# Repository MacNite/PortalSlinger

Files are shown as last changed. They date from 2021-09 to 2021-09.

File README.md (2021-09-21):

# PortalSlinger
PortalSlinger is an OpenSource Large Format 3D printer. The Idea was to built a large format 3D printer in the most affordable way without sacrificing to much performance. I've tested successfully teste print speeds of up to 100mm/s.

# supported by https://www.cr-3d.de

* Built Volume: 	850 mm x 400 mm x 280 mm
* Frame:          Aluminium Extrusion 3060 Slot 8
* Hotend:       	Trianglelab Volcano, Nozzle 0.8mm
* Filament:     	1,75mm, PLA & PETG
* Extruder:     	Bondtech BMG
* Bed Leveling: 	Mesh Bed Leveling with BLTouch
* Built Plate:    Caste Aluminium Plate, t = 10mm
* Print Surface:  ULTEM PEI 1000
* Heated Bed:   	2x 750W (total 1500W), 230V, up to 100C
* Connectivity:  	7“ Touch Screen, Wifi
* Controller:   	Duet Wifi
* PSU:          	Meanwell LRS-350-24
* Current Draw: 	< 8 A / < 1850 W, filtered C14 inlet with 5x20 (10A) Fuse
* Coldend Fan:  	40x20mm, 24V axial fan
* Partcooling   	4010, 24V radial fan (2 Pcs)
* Electronic:   	PSU fan and 4020 radial fan
* Linear Motion:  x: MGN12H (L=475mm), Y: HGH15CA (L=1000mm), Z: 10mm smooth rod with LMK10LUU
* Axis Movement:  x & y: 10mm GT2 belts, z: TR10x2 spindle

Find the Fusion360 model for your viewing/download pleasure here (you can download the F360 model through this link as well):

https://a360.co/3zzRa0U

.stp / .iges Files are not provided via GITHUB because they are to large (more than 25mb). You can download .stp / .iges files via the Autodesk Fusion 360 link provided above.

There is an untested / unbuilt beta-Version-CAD-Model available - this is only for "what is to come", major changes include re-positioning of y-belts, different tool head (not yet desgined) and MGN9H rails for the z-axis. Proceed with caution! https://a360.co/2XAqKi2

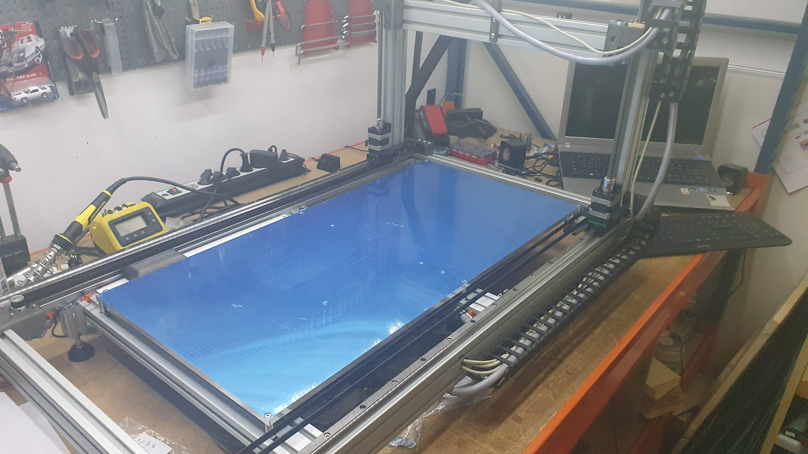
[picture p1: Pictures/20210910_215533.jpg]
PortalSlinger


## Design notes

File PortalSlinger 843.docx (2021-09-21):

# Technische Dokumentation

# Portal Slinger 843

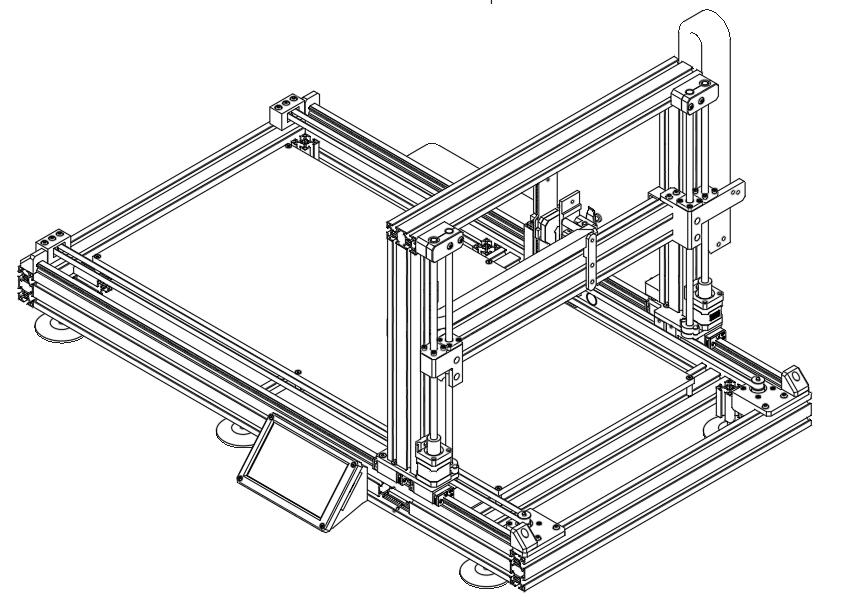
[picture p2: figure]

# 1. Technische Daten

Bauraum | 850 mm x 400 mm x 280 mm
Bauart Rahmen | Aluminium-Profile 3060 Nut 8
Hotend | Trianglelab Volcano, Düse 0.8mm
Filament | 1,75mm, PLA & PETG
Extruder | Bondtech BMG
Bed Leveling | Mesh Bed Leveling mit BLTouch (CE)
Bauplattform | Aluminium Plangefräst, t = 10mm
Druckoberfläche | ULTEM PEI 1000
Heizbett | 2x 750W (insg. 1500W), 230V, bis ca. 90°C
Konnektivität: | 7“ Touch Screen, Wifi
Steuerkarte | Duet Wifi
Netzteil | Meanwell LRS-350-24
Leistungsaufnahme | < 8 A bzw < 1850 W, C14 Kaltgerätebuchse mit Filter und 5x20 (10A) Sicherung
Coldend Lüfter | 40x20mm, 24V Axial-Lüfter
Bauteilkühlung | 4010, 24V Radial-Lüfter (2 Stk.)
Elektronik Kühlung | Integrierter Lüfter Netzteil 4020, 24V Radial-Lüfter
Linearführungen | X: MGN12H Y: HGH15CA Z: 10mm Welle mit LMK10LUU

# 2. Verkabelung des Druckkopfes

Kabelbelegung
y-Gantry | | | | | | Kabel
Stepper z1 | A+ | A- | B+ | B- | | Unitronic LIYY 4x0,34
| braun | grün | gelb | weiß
Stepper z2 | A+ | A- | B+ | B- | | Unitronic LIYY 4x0,34
| braun | grün | gelb | weiß
Stepper x | A+ | A- | B+ | B- | | Unitronic LIYY 4x0,34
| braun | grün | gelb | weiß
Stepper e0 | A+ | A- | B+ | B- | | Ölflex YSLY-JZ 25x0,5
| 4 | 5 | 6 | 7
Filament Runout | 5V | GND | S
| 21 | 22 | 23
F0 | 24V | GND
| 8 | 9
F1 | 24V | GND
| 19 | 20
H0 | 24V | GND
| 2 & 3 | 12 & 13
T0 | S | S
| 10 | 11
BLTouch | 5V | GND | Control | S | GND
| 14 | 15 | 16 | 17 | 18

# 3. Ersatzteile

Pos | Bauteil | Bestell-Link | alternativ
1 | Hotend, E3D V6, 24V, 1.75mm | https://s.click.aliexpress.com/e/_AeW5l4 | https://e3d-online.com/products/volcano-hotend
2 | BLTouch (ABL) | https://s.click.aliexpress.com/e/_A2BXyi | https://www.3djake.de/antclabs/bltouch-nivellierungssensor
3 | SSR (2 Stück) | https://www.cr3d.de/produkt/solid-state-relais-10a/ | -
4 | Extruder Bondtech BMG | https://s.click.aliexpress.com/e/_AneSdo | https://www.cr3d.de/produkt/xtruder/
5 | GT2 Idler, 25 Zähne, Riemen w=10mm, Bohrung 5mm, mit Zähnen (3 Stück) | https://s.click.aliexpress.com/e/_Aq2wyQ | -
6 | GT2 Pulley, 25 Zähne, Riemen w=10mm, Bohrung 5mm, mit Zähnen | https://s.click.aliexpress.com/e/_AfUzRY | -
7 | Zahnriemen GT2, B=10mm, L = 6 m | https://s.click.aliexpress.com/e/_9HzY4A | -
8 | Führung x-Achse (MGN12H, L = 475mm) | https://de.aliexpress.com/item/32829826159.html?spm=a2g0s.8937460.0.0.145d2e0eUGBRX5 | -
8 | Führung y-Achse (HGR15 CA, 2 Stück, L = 1000mm) | https://de.aliexpress.com/item/32961758272.html?spm=a2g0s.8937460.0.0.68d82e0e5REzLT | -
9 | Display PanelDue 7i | https://s.click.aliexpress.com/e/_9uxG9o
10 | Controller Duet Wifi | https://s.click.aliexpress.com/e/_A2KRGw | https://www.cr3d.de/produkt/duet-2-wifi/
11 | Silikon Heizmatte ( 2 Stück, 220V, 750W, Schwarz, 400x400mm) | https://s.click.aliexpress.com/e/_9j0cQE | -
12 | NEMA17 Schrittmotor (17HS15-1504S-X1) | https://s.click.aliexpress.com/e/_AU5lhU | -
13 | Druckoberfläche ULTEM PEI1000 850x410mm, nur auf Anfrage | https://www.muellerbestellung.de/TC00421-3D-ES-Ultem-1000-Polyetherimid-3D-Druck-Folie-Schwarz-einseitig-selbstklebend

# 4. Riemenspanner

x-Achse:

Wenn man „vor“ dem Drucker steht (auf der Seite mit Display und Kaltgeräteanschluss) auf der Rückseite des Tool-Heads, M5 Linsenkopfschraube. Kann mit einem 2,5mm Inbusschlüssel nachgezogen werden.

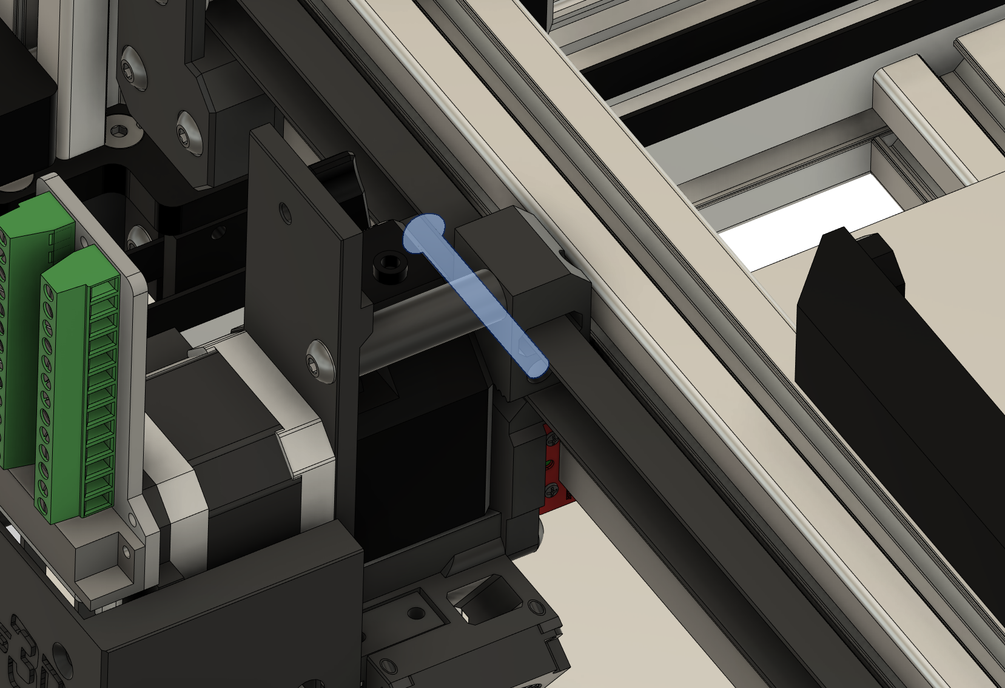
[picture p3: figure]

y-Achse:

Unterhalb des Portals auf beiden Seiten. M5 Linsenkopfschraube. Kann mit einem 2,5mm Inbusschlüssel nachgezogen werden.

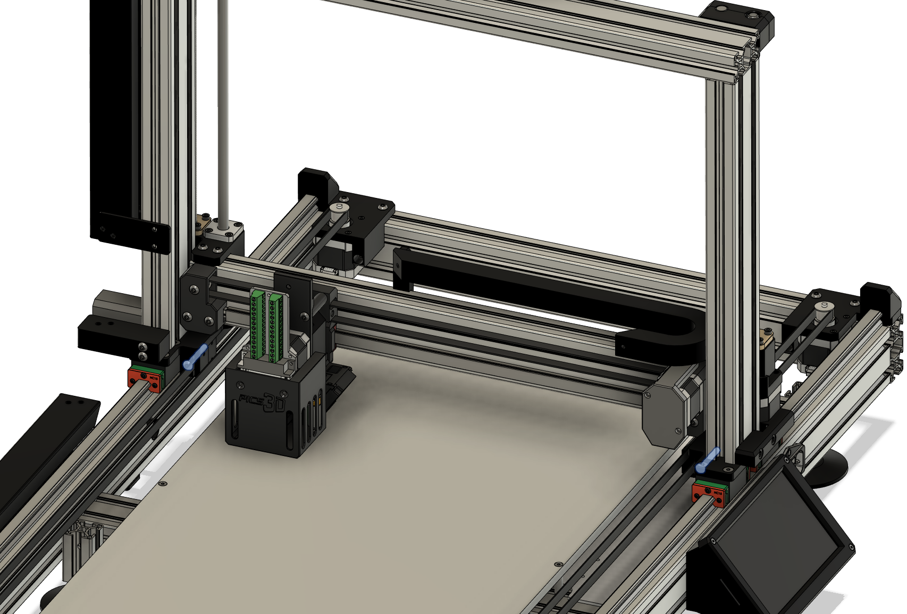
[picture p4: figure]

# 5. Druckdateien und Source-Files

Falls mal etwas am Drucker defekt ist und neu gedruckt oder anders gefertigt werden muss, sind die zugehörigen Dateien auf der Github-Seite zu finden:

https://github.com/MacNite/PortalSlinger

5 M. Nitschke Stand: 21.09.2021

Portal Slinger 843 3D Drucker – Dokumentation

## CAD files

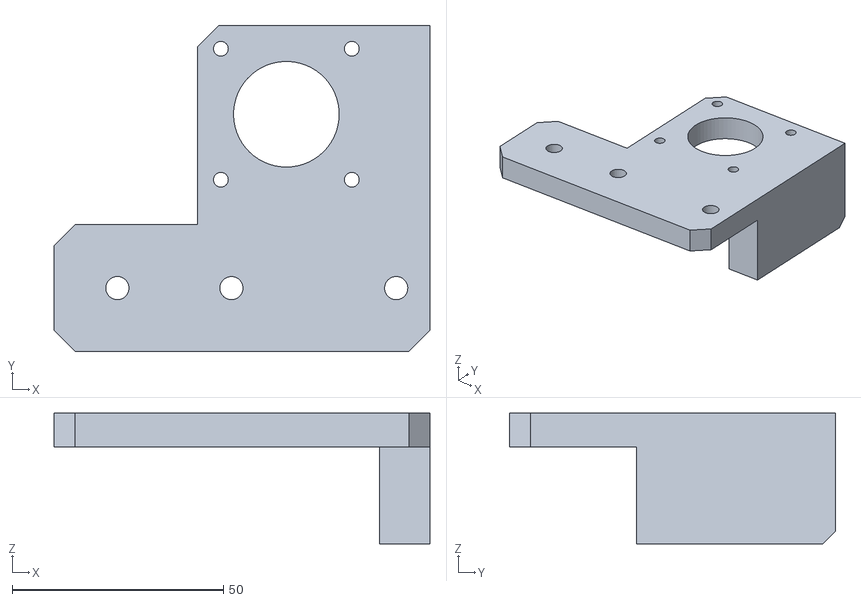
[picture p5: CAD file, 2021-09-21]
STL/y_Stepper_Mount_B_x1.stl
89.0 x 77.2 x 31.0

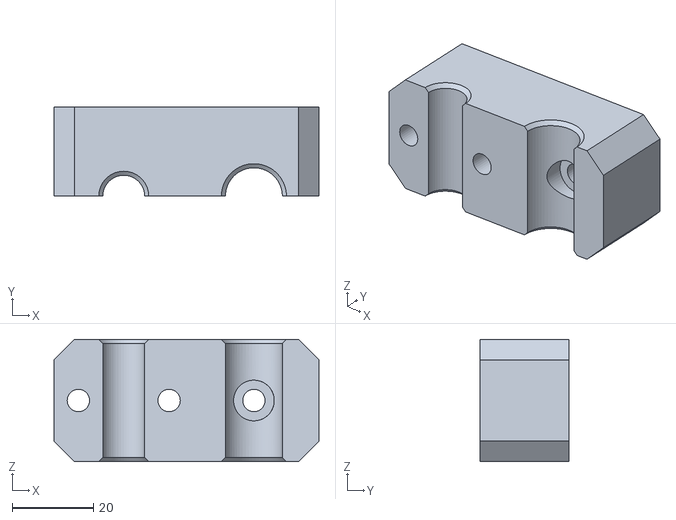
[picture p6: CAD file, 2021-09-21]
STL/z_Rot_Top_Mount_A_x2.stl
65.1 x 22.0 x 30.0

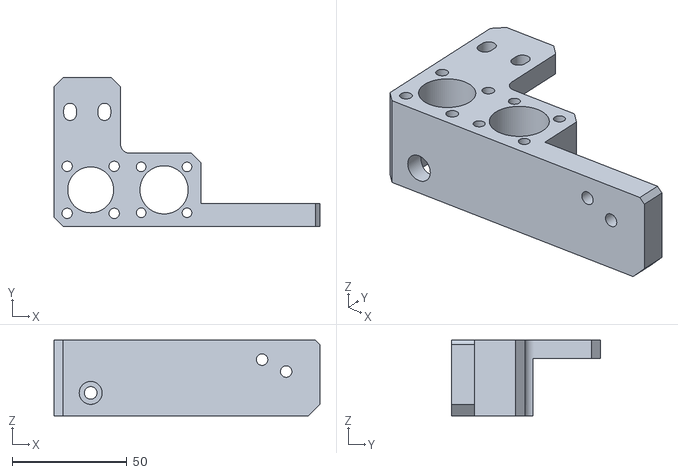
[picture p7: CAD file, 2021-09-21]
STL/z_Carriage_A_x1.stl
116.0 x 65.0 x 33.0

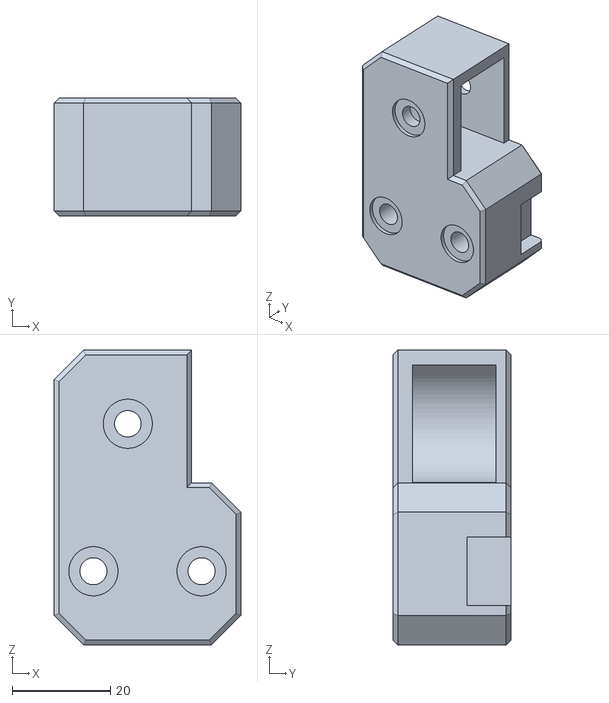
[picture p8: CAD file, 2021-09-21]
STL/x_Idler_Mount_x1.stl
38.0 x 24.0 x 60.0

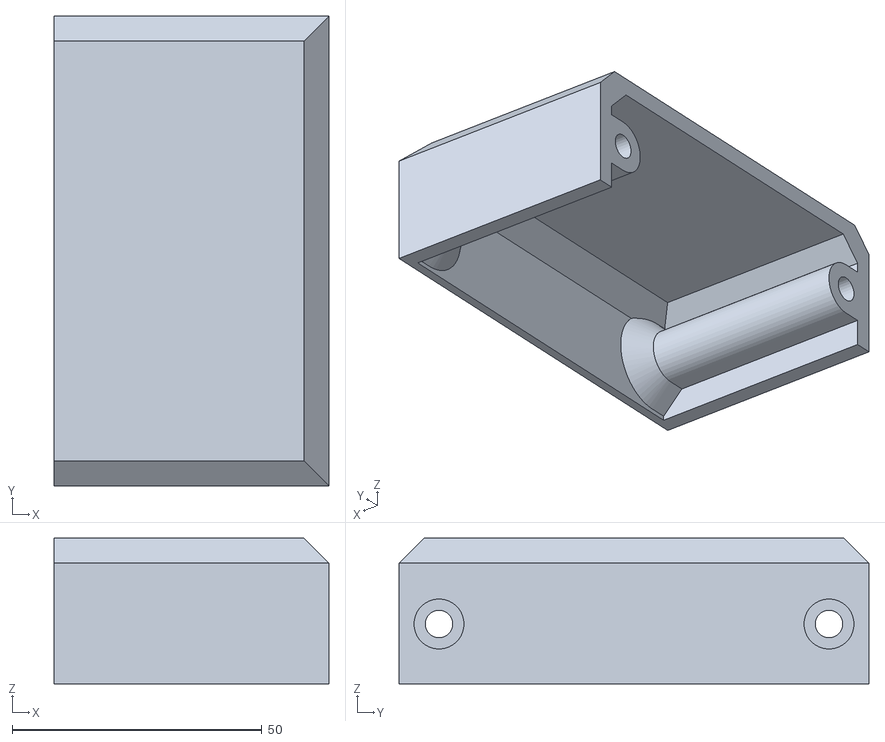
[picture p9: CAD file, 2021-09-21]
STL/IEC_Cover_x1.stl
55.0 x 94.0 x 29.2

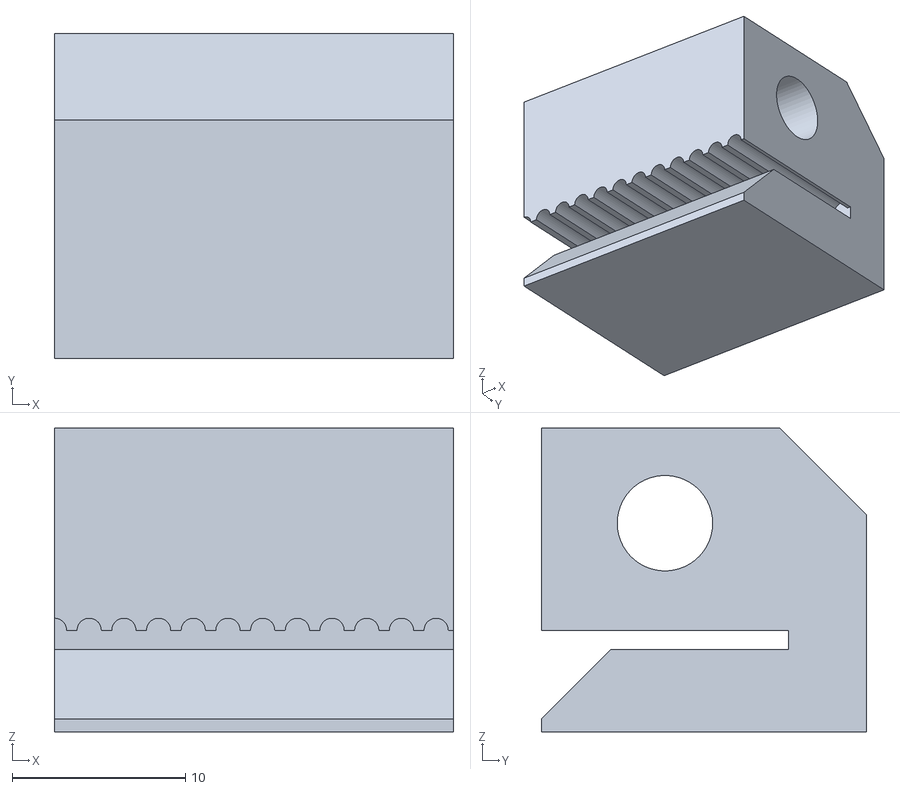
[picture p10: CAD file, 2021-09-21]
STL/x_Belt_Tensioner_x1.stl
23.0 x 18.8 x 17.5

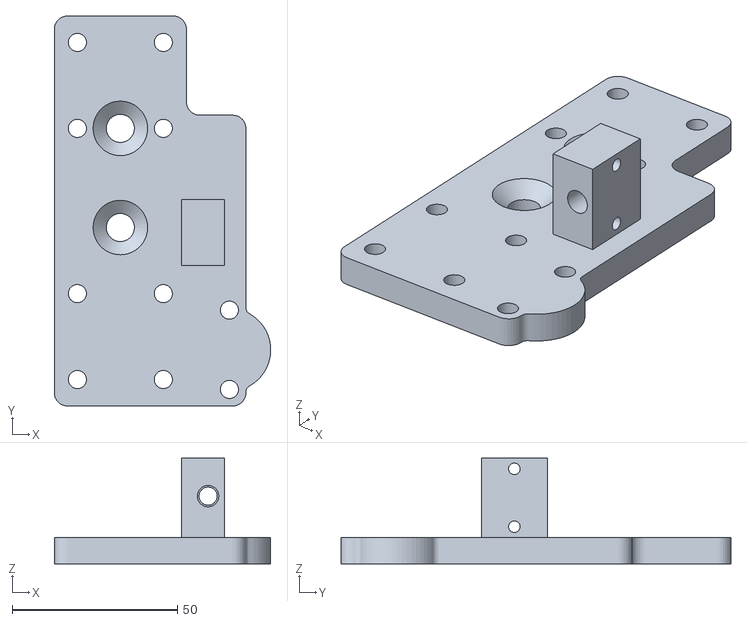
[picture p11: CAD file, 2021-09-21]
STL/y_Carriage_B_x1.stl
65.5 x 118.0 x 32.0

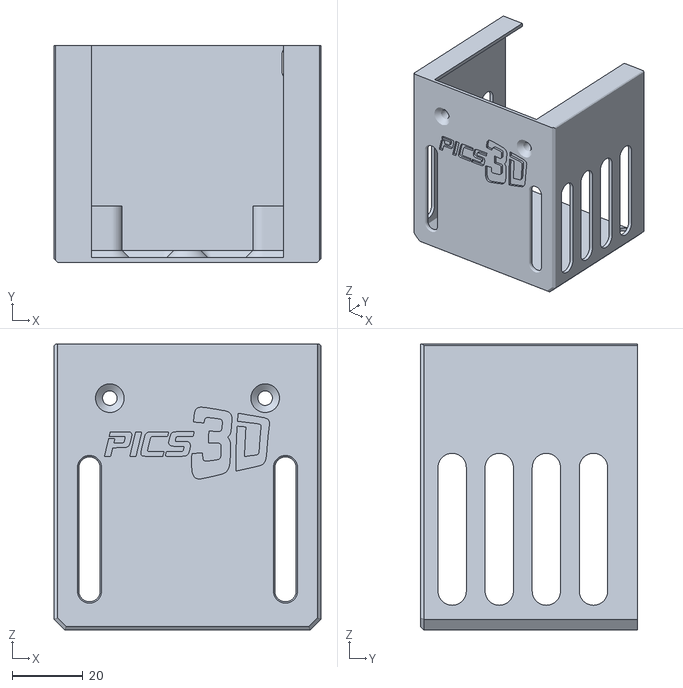
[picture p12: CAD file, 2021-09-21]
STL/x_Carriage_DSUB_Cover_x1.stl
75.5 x 61.5 x 80.9

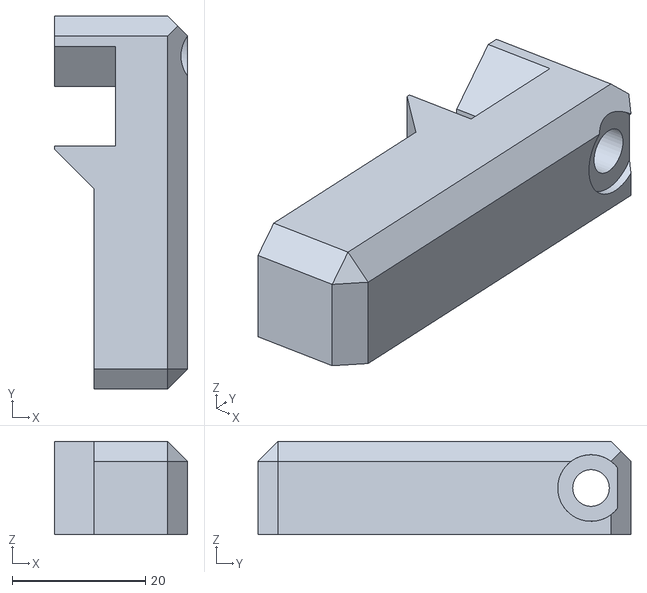
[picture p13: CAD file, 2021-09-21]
STL/z_Stepper_Cable_Cover_Dragchain_x1.stl
20.0 x 56.0 x 14.0

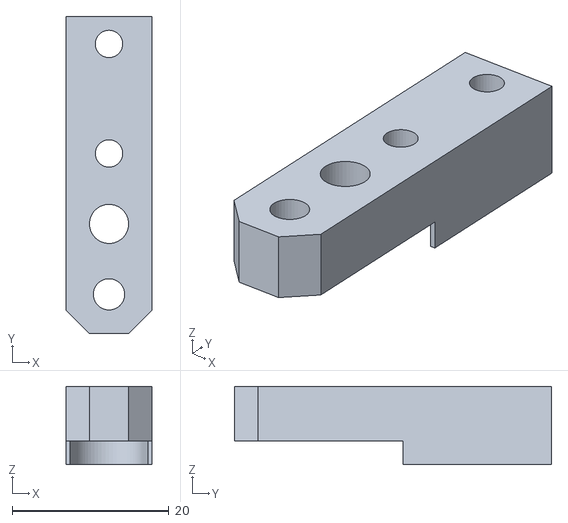
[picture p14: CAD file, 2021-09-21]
STL/BLTouch_Mount_x1.stl
11.0 x 40.5 x 10.0

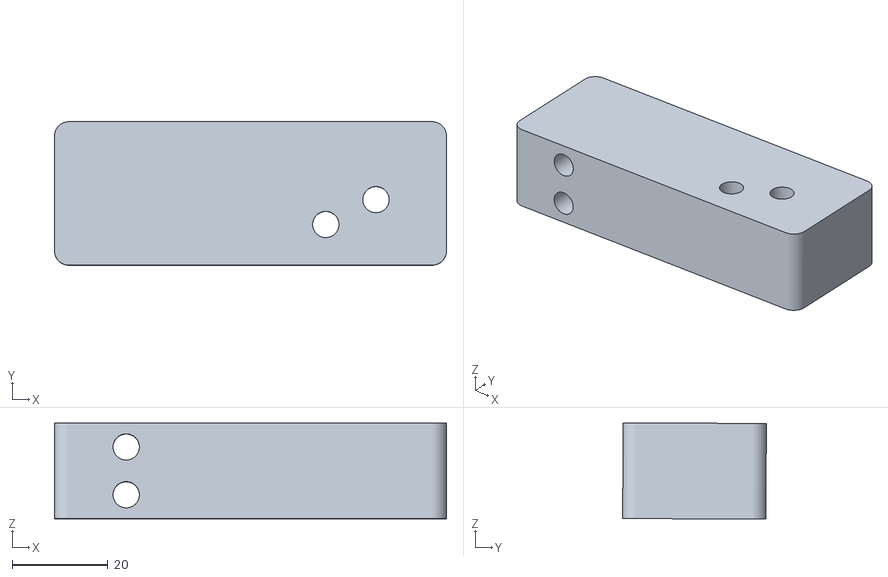
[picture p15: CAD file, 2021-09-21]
STL/Dragchain_Mount_x1.stl
82.0 x 30.0 x 20.1

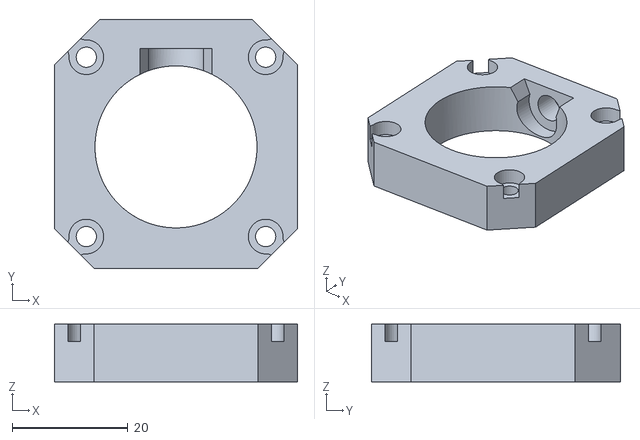
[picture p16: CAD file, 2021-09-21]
STL/z_Stepper_Mount_x2.stl
42.0 x 43.0 x 10.0

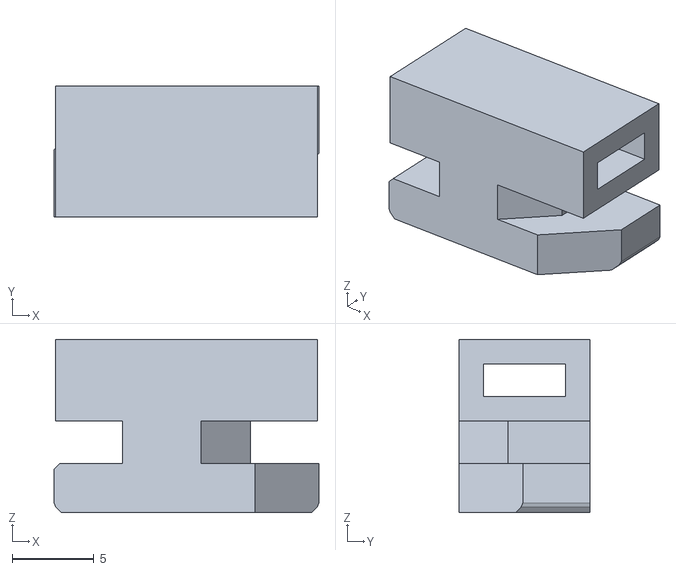
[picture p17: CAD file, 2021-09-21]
STL/3030clipA.stl
16.2 x 8.00 x 10.6

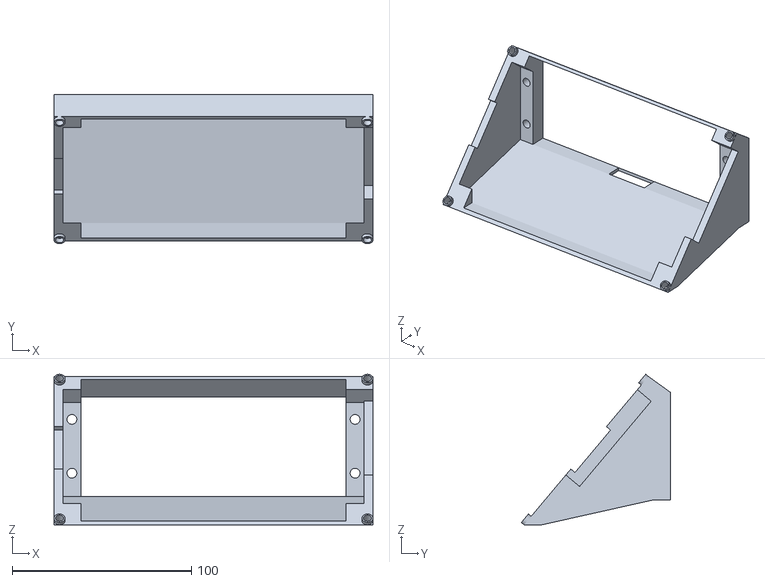
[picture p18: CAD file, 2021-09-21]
STL/PanelDue_Mount_x1.stl
178.0 x 83.3 x 84.0

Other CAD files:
STL/y_Stepper_Mount_A_x1.stl
STL/y_Carriage_A_x1.stl
STL/x_stepper_cable_cover_x1.stl
STL/x_Carriage_x1.stl
STL/3030clipB.stl
STL/DSUB_Spacer_x1.stl
STL/Dragchain_Mount_x_x1.stl
STL/Drill_Jig_A_x1.stl
STL/Drill_Jig_B_x1.stl
STL/HGR_Centering_Jig_x6.stl
STL/IEC_Drill_Jig_x1.stl
STL/M3x15 Spacer x2.stl
STL/PanelDue_Cover_x1.stl
STL/Passthrough_x1.stl
STL/Spacer_x7.stl
STL/Stopper_x4.stl
STL/Tool_Head_x1.stl
STL/Tool_Spacer_x1.stl
STL/Wago_222_Holder.obj
STL/Z_Rod_Top_cover_x2.stl
STL/x_Carriage_Belt_Tensioner.stl
STL/x_Carriage_DSUB_Mount_x1.stl
STL/x_Stepper_Mount_x1.stl
STL/y_Belt_Clamp_x4.stl
STL/y_Belt_Tensioner_x2.stl
STL/y_Idler_Mount_x2.stl
STL/z_Carriage_B_x1.stl
STL/z_Rod_Bottom_Mount_x2.stl
STL/z_Rot_Top_Mount_B_x2.stl
STL/z_Stepper_Cable_Cover_x1.stl
STL/z_Stepper_cover.stl

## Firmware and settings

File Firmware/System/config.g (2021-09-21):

; Configuration file for Duet WiFi (firmware version 3)
; executed by the firmware on start-up
;
; generated by RepRapFirmware Configuration Tool v3.3.0 on Wed Aug 11 2021 08:50:32 GMT+0200 (Mitteleuropäische Sommerzeit)

; General preferences
M575 P1 S1 B57600                               ; enable support for PanelDue
G90                                             ; send absolute coordinates...
M83                                             ; ...but relative extruder moves
M550 P"PortalSlinger 843"                       ; set printer name

; Network
M552 S1                                         ; enable network
M586 P0 S1                                      ; enable HTTP
M586 P1 S0                                      ; disable FTP
M586 P2 S0                                      ; disable Telnet

; Drives
M569 P0 S0                                      ; physical drive 0 goes backwards
M569 P1 S1                                      ; physical drive 1 goes forwards
M569 P2 S1                                      ; physical drive 2 goes forwards
M569 P3 S1                                      ; physical drive 3 goes forwards
M569 P4 S0                                      ; physical drive 4 goes backwards
M584 X3 Y2 Z0:1 E4                              ; set drive mapping
M350 X16 Y16 Z16:16 E16 I1                   	; configure microstepping with interpolation
M92 X64 Y64 Z1600:1600 E415                  	; set steps per mm
M566 X900 Y900 Z60:60 E180                  	; set maximum instantaneous speed changes (mm/min)
M203 X6000 Y6000 Z600:600 E3000           		; set maximum speeds (mm/min)
M201 X1000 Y1000 Z20:20 E500               		; set accelerations (mm/s^2)
M906 X800 Y1200 Z1000:1000 E800 I30          	; set motor currents (mA) and motor idle factor in per cent
M84 S30                                         ; Set idle timeout

; Axis Limits
M208 X0:400 Y0:850 Z0:285                       ; set axis minima
M671 X-80:480 Y450:450 S5						; lead screw position - max adjustment 5mm

; Endstops
M574 X2 S3                                      ; configure sensorless endstop for high end on X
M574 Y2 S3                                      ; configure sensorless endstop for high end on Y
M574 Z1 S2                                      ; configure z-probe for low end on Z

; Stall Detection
M915 X S3 R0									; sensorless homing on x, sensitivity S=3, R=0: Only use for homing
M915 Y S5 R0									; sensorless homing on y, sensitivity S=5, R=0: Only use for homing

; Z-Probe
M950 S0 C"exp.heater3"                          ; create servo pin 0 for BLTouch
M558 P9 C"^zprobe.in" H5 F600 T6000             ; set Z probe type to bltouch and the dive height + speeds
G31 P500 X33 Y35 Z1.6                           ; set Z probe trigger value, offset and trigger height
M557 X53:390 Y65:880 P3:5                       ; define mesh grid
;M557 X40:370 Y40:800 P6:10                     ; define mesh grid very fine

; Heaters & Temp Sensors
M308 S0 P"bedtemp" Y"thermistor" T100000 B4725 C7.06e-8  ; configure sensor 0 as thermistor on pin bedtemp
M950 H0 C"bedheat" T0                           ; create nozzle heater output on bedheat and map it to sensor 0
M307 H0 B0 S1.00                                ; disable bang-bang mode for heater  and set PWM limit
M143 H0 S260                                    ; set temperature limit for heater 0 to 260C

M308 S1 P"e0temp" Y"thermistor" T100000 B4092   ; configure sensor 1 as thermistor on pin e0temp
M950 H1 C"e0heat" T1                            ; create nozzle heater output on e0heat and map it to sensor 1
M307 H1 B0 S1.00                                ; disable bang-bang mode for heater  and set PWM limit
M143 H1 S100                                    ; set temperature limit for heater 1 to 100C
M308 S2 P"e1temp" Y"thermistor" T100000 B4092   ; configure sensor 2 as thermistor on pin e1temp
M950 H2 C"e1heat" T2                            ; create nozzle heater output on e1heat and map it to sensor 2
M307 H2 B0 S1.00                                ; disable bang-bang mode for heater  and set PWM limit
M143 H2 S100                                    ; set temperature limit for heater 2 to 100C

M140 P1 H1                                     ; use heater 1 for heated bed 1
M140 P2 H2                                     ; use heater 2 for heated bed 2

M308 S3 Y"mcu-temp" A"MCU"					    ; configure sensor 3 for mcu temp
M308 S4 Y"drivers" A"drivers"				    ; configure sensor 4 for drivers

; Fans
M950 F0 C"fan0" Q500                            ; create fan 0 on pin fan0 and set its frequency
M106 P0 C"Part Cooling" S0 H-1                  ; set fan 0 name and value. Thermostatic control is turned off
M950 F1 C"fan1" Q500                            ; create fan 1 on pin fan1 and set its frequency
M106 P1 C"Coldend" S1 H0 T45                    ; set fan 1 name and value. Thermostatic control is turned on
M950 F2 C"fan2" Q500                            ; create fan 2 on pin fan2 and set its frequency
M106 P2 C"Electronics" S1 H3:4 T40:50           ; set fan 2 name and value. Thermostatic control is turned on

; Tools
M563 P0 D0 H0 F0                                ; define tool 0
G10 P0 X0 Y0 Z0                                 ; set tool 0 axis offsets
G10 P0 R0 S0                                    ; set initial tool 0 active and standby temperatures to 0C

; Miscellaneous
M575 P1 S1 B57600                               ; enable support for PanelDue
M501                                            ; load saved parameters from non-volatile memory
T0                                              ; select first tool on startup
